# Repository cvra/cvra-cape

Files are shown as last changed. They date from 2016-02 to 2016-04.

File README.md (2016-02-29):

# CVRA cape

A Beaglebone black extension board for robots used at [CVRA](http://www.cvra.ch/).

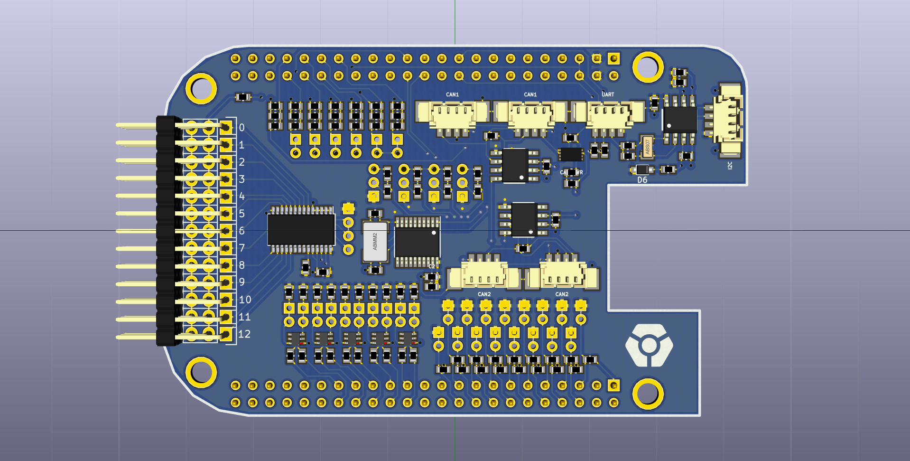
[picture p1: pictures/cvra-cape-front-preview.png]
Board Layout (Front view)

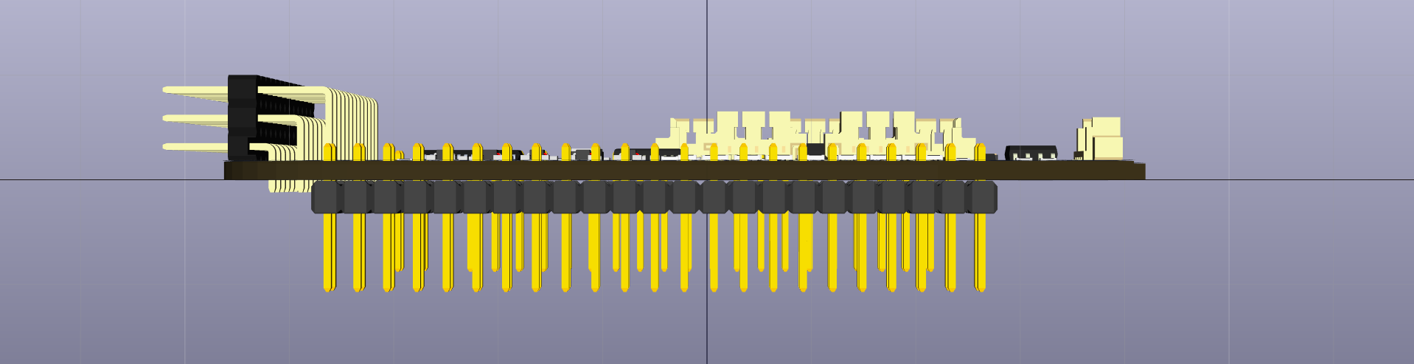
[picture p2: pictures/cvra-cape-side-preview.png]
Board Layout (Side view)


## Features
- 2x CAN interfaces with transceivers
    - 1x over native CAN peripheral
    - 1x over CAN-SPI chip
- 16x PWM outputs (using a PCA9685 chip over I2C)
    - 13x to control servo motors
    - 1x to control an RGB LED
- 7x analog inputs with voltage dividers and option to power (3-pin connector)
    - 1x analog Lidar 1D input
    - 1x battery voltage sense
    - 1x CAN-bus voltage sense
    - 4x free
- 18x digital inputs with voltage dividers and option to power (3-pin connector)
- 10x digital outputs (LEDs) with NPN stage to draw 10-100mA
- Power the BBB over the CAN-bus or over USB (switch)
- 1x I2C connector
- 1x UART connector
- 1x RTC with battery soldered directly on the cape

## Notes

### PWM
The PWM outputs are provided by a PWM chip controlled over I2C (PCA9685).

### CAN
There are 2 CAN interfaces on the cape. We use one. The other CAN uses an SPI (TBD).
- `CAN1` uses the `DCAN1` interface on the Beaglebone
    * `CAN1_RX` is on pin `P9.24`
    * `CAN1_TX` is on pin `P9.26`

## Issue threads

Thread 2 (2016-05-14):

Changes for revB

SyrianSpock, 2016-05-14:
- No 5V CAN bus power protection (too much current limiting, Beaglebone's protection is enough)
- Fix RX/TX inversion on CAN1 tranceiver

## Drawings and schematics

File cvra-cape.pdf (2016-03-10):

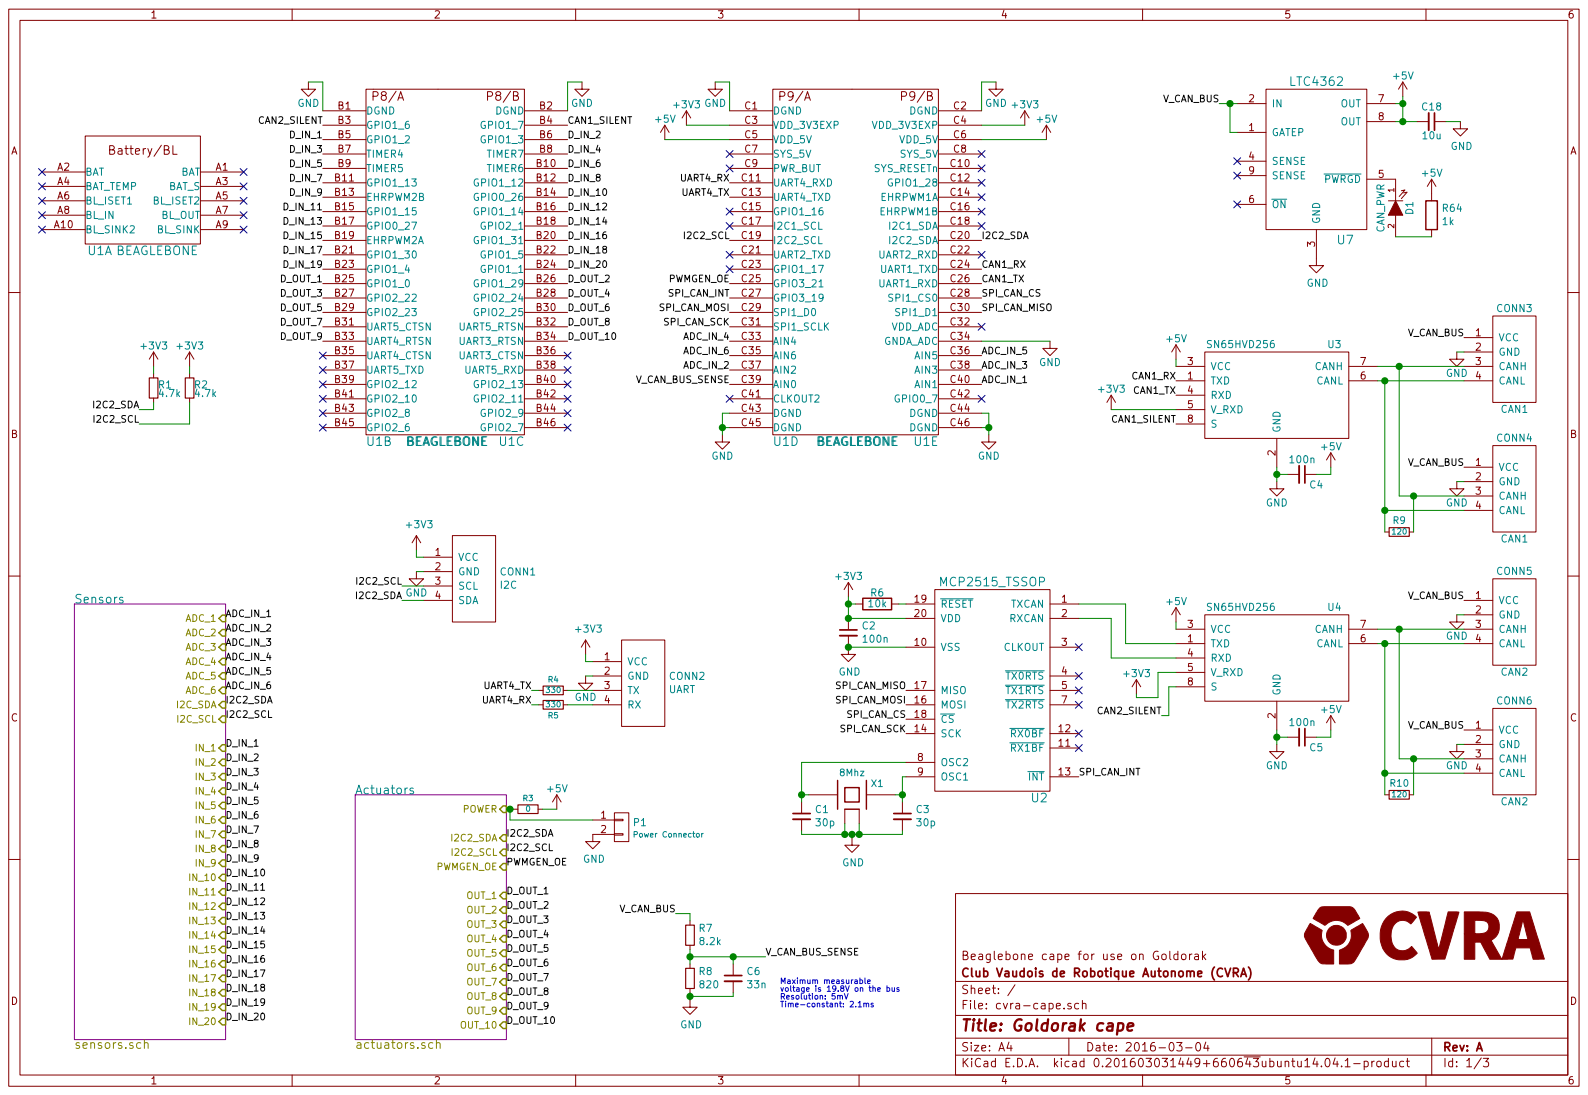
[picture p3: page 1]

3 SENSE 4 PWRGD 5 ON 6 OUT 7 OUT 8 SENSE 9 U7

2 VCC 3 RXD 4 V_RXD 5 CANL 6 CANH 7 S

Beaglebone cape for use on Goldorak
File: cvra-cape.sch Sheet: / Club Vaudois de Robotique Autonome (CVRA)

Maximum measurable voltage is 19.8V on the bus Resolution: 5mV

Id: 1/3 Title: Goldorak cape

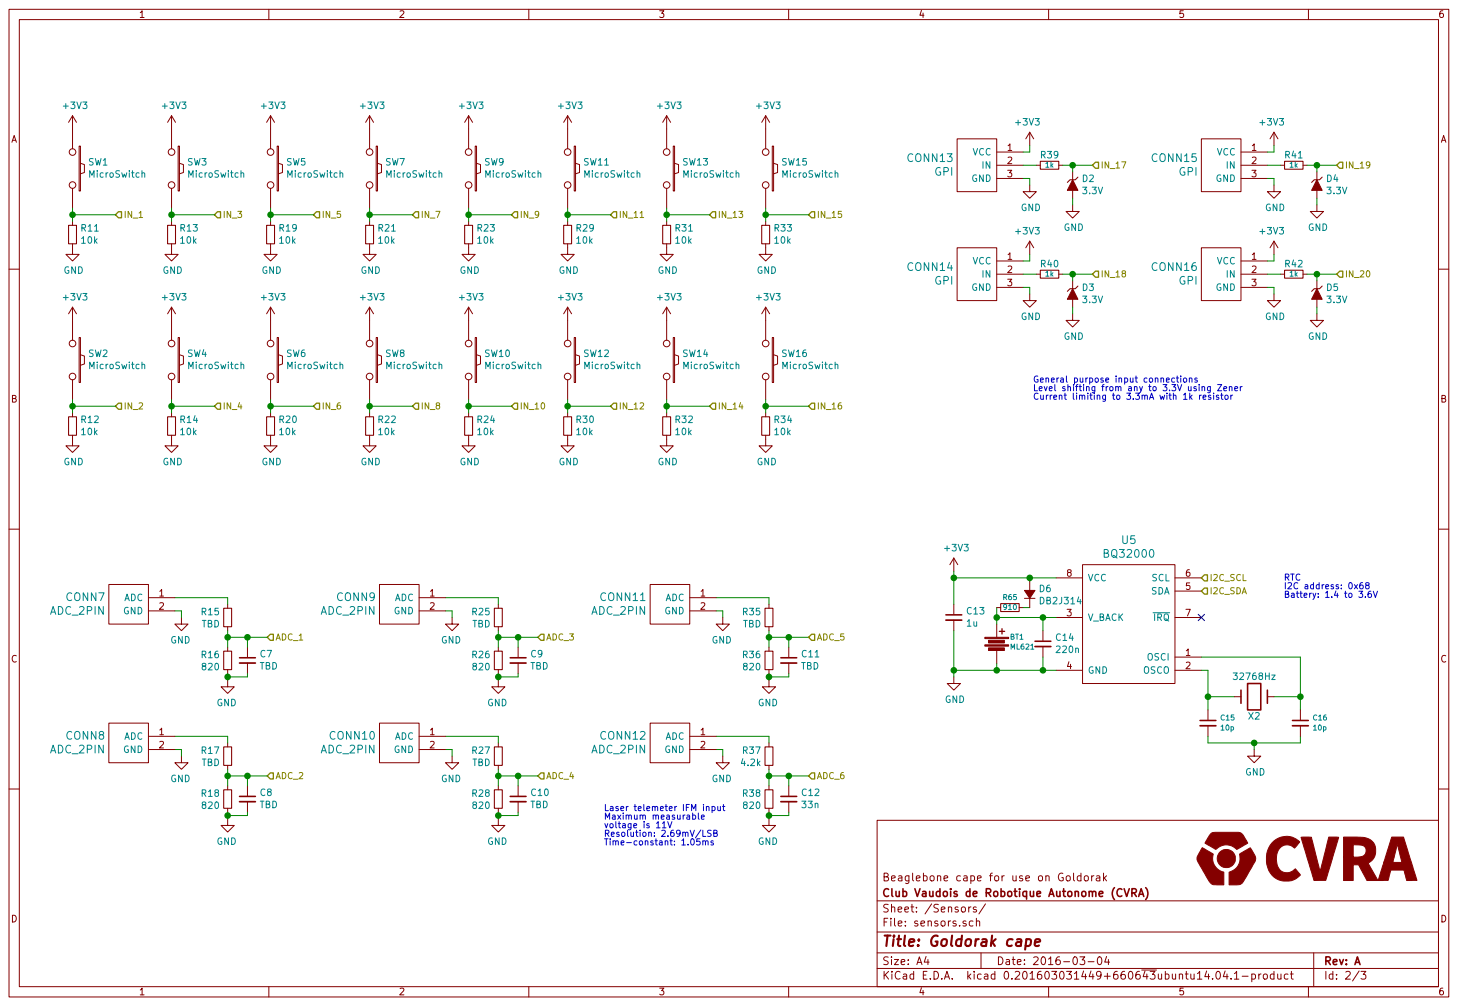
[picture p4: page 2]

IN_18 General purpose input connections Level shifting from any to 3.3V using Zener Current limiting to 3.3mA with 1k resistor C7 TBD

Beaglebone cape for use on Goldorak ADC_1 R15 TBD

Laser telemeter IFM input Maximum measurable
voltage is 11V Resolution: 2.69mV/LSB

File: sensors.sch Sheet: /Sensors/ Club Vaudois de Robotique Autonome (CVRA)

Id: 2/3 Title: Goldorak cape

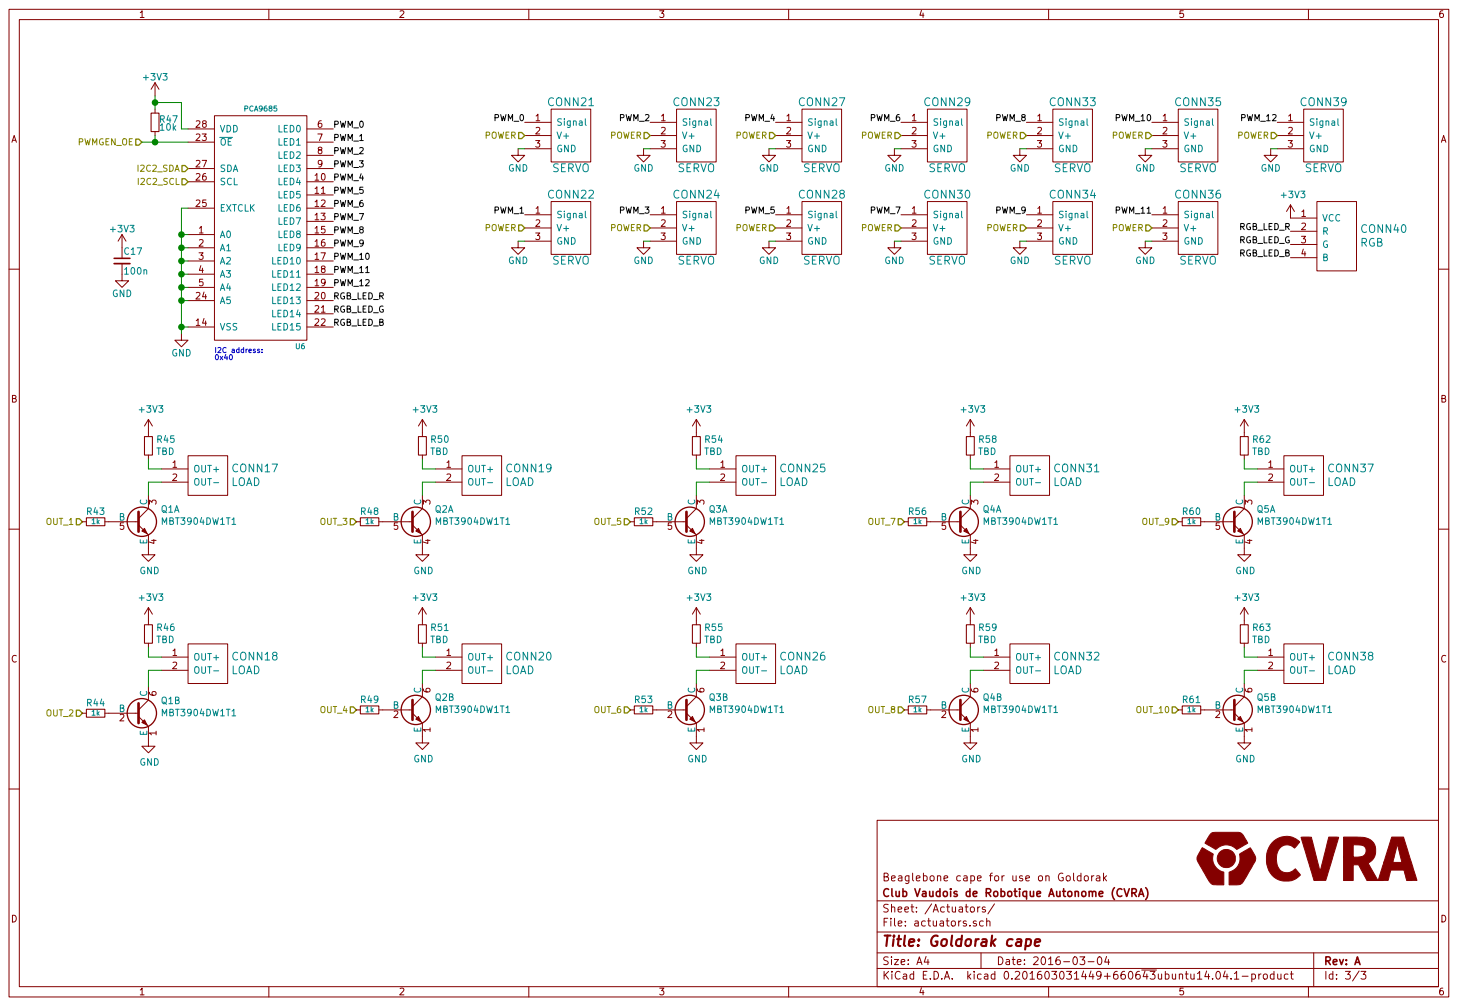
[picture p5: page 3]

Beaglebone cape for use on Goldorak
File: actuators.sch Sheet: /Actuators/ Club Vaudois de Robotique Autonome (CVRA)

Id: 3/3 Title: Goldorak cape

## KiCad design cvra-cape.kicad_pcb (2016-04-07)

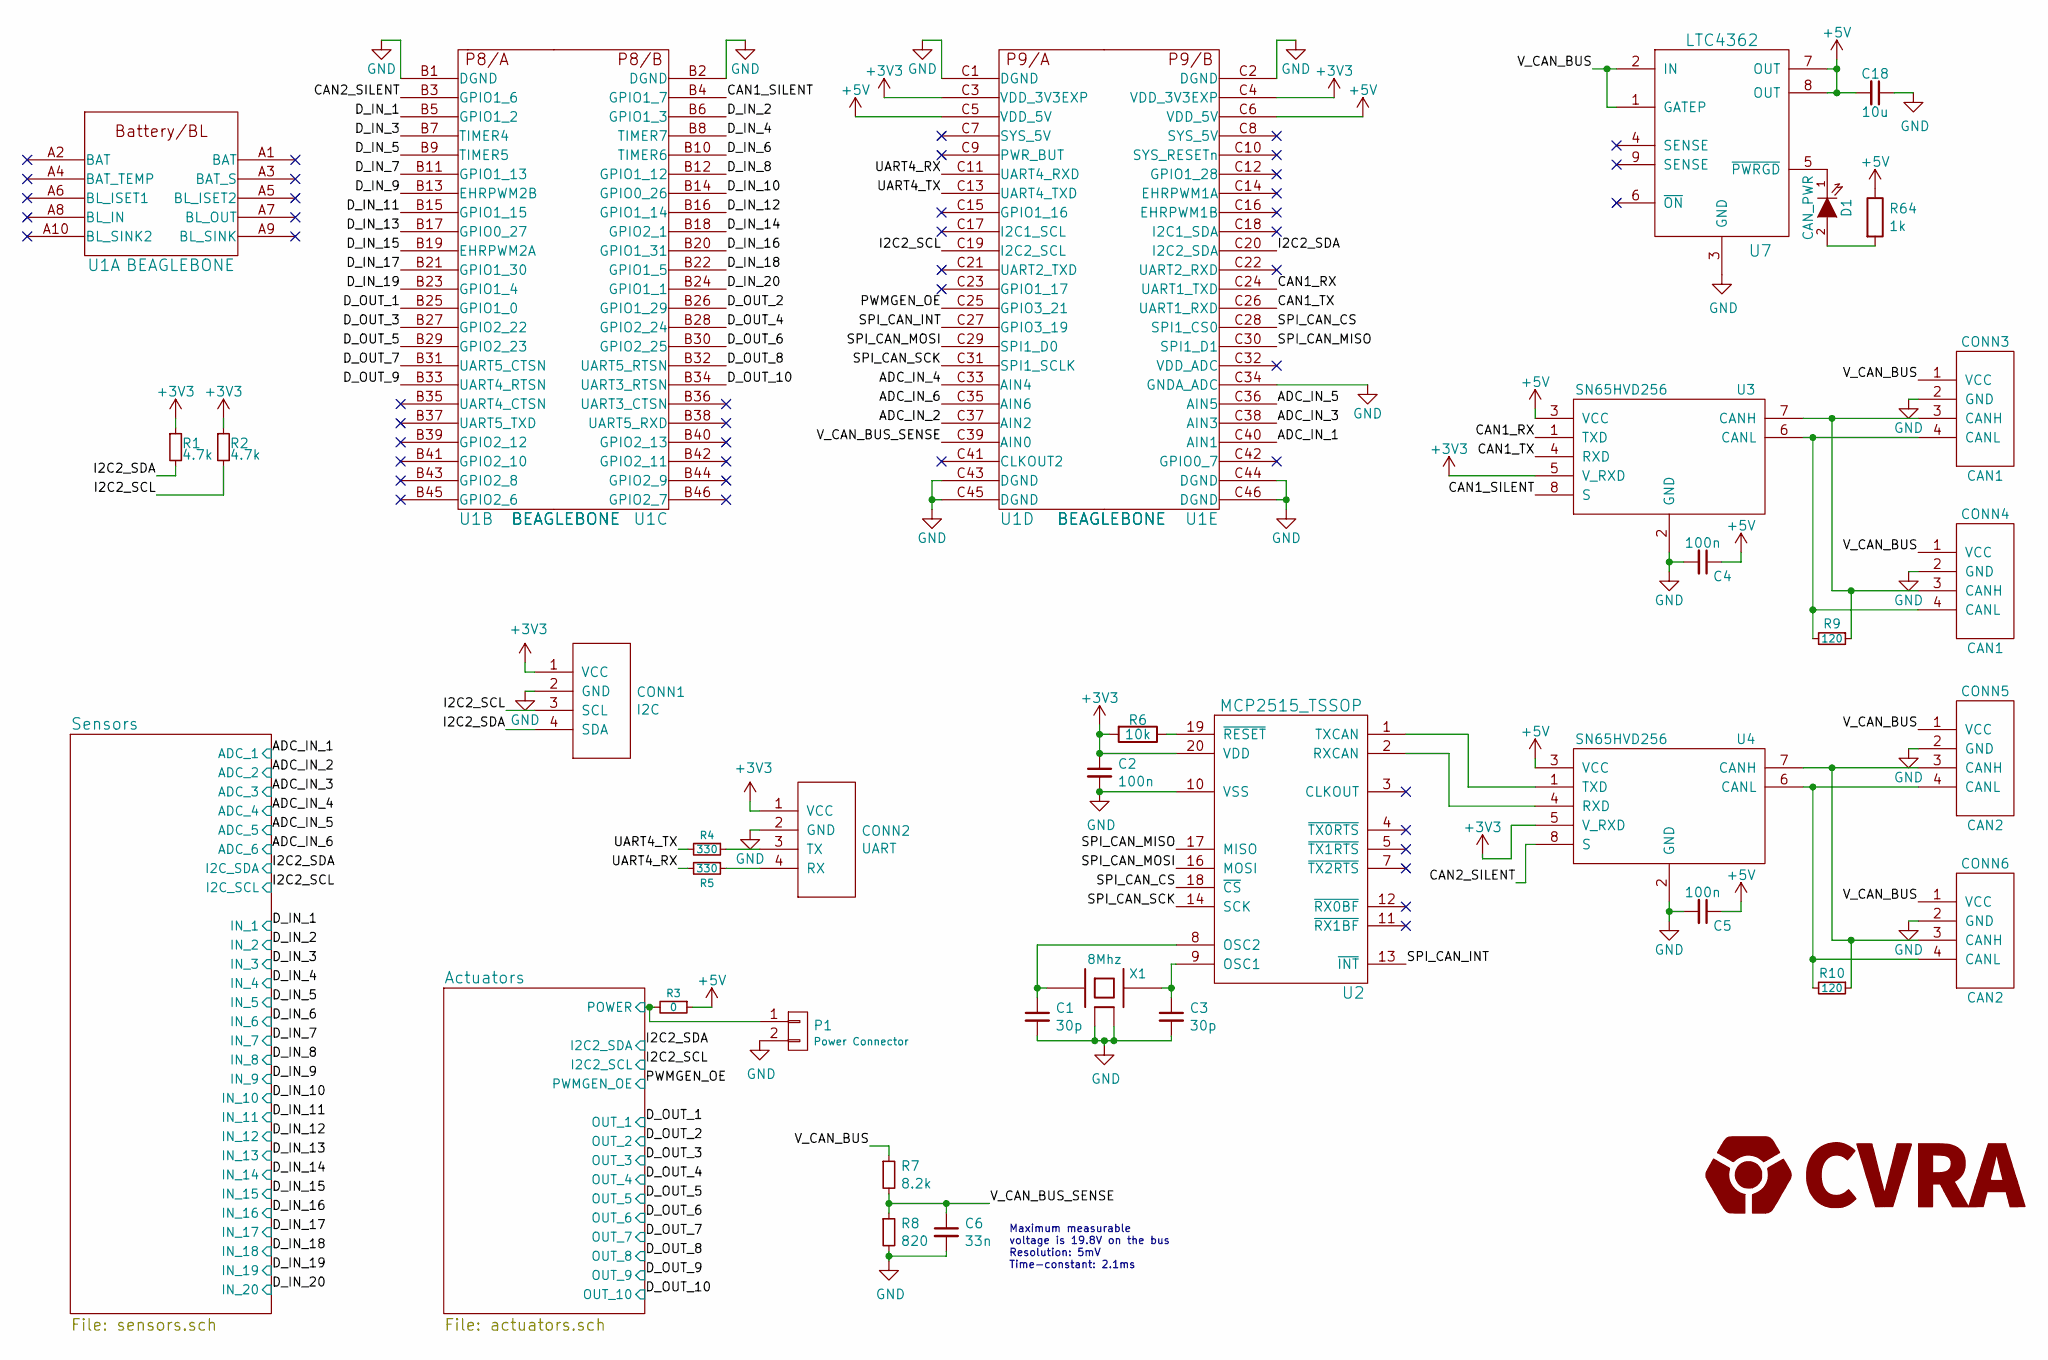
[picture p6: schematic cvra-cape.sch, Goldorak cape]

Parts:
C1, C3: 30p; _0603
C2, C4, C5: 100n; _0603
C6: 33n; _0603
C18: 10u; _0603
CONN1: I2C; _Molex-PicoBlade-SMD-4
CONN2: UART; _Molex-PicoBlade-SMD-4
CONN3, CONN4: CAN1; _Molex-PicoBlade-SMD-4
CONN5, CONN6: CAN2; _Molex-PicoBlade-SMD-4
D1: CAN_PWR; _0603
P1: Power Connector; Pin_Header_Straight_1x02
R1, R2: 4.7k; _0603
R3: 0; _0603
R4, R5: 330; _0603
R6: 10k; _0603
R7: 8.2k; _0603
R8: 820; _0603
R9, R10: 120; _0603
R64: 1k; _0603
U1: BEAGLEBONE
U2: MCP2515_TSSOP; TSSOP-20_4.4x6.5mm_Pitch0.65mm
U3, U4: SN65HVD256; _SO-8
U7: LTC4362; DFN_8-Lead_2mmx3mm
X1: 8Mhz; XTAL_ABMM2

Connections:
+3V3: C2.1, CONN1.1 (VCC), CONN2.1 (VCC), R1.1, R2.1, R6.2, U1.C3 (VDD_3V3EXP), U1.C4 (VDD_3V3EXP), U2.20 (VDD), U3.5 (V_RXD), U4.5 (V_RXD); also elsewhere on the board
+5V: C4.1, C5.1, C18.2, R3.1, R64.1, U1.C5 (VDD_5V), U1.C6 (VDD_5V), U3.3 (VCC), U4.3 (VCC), U7.7 (OUT), U7.8 (OUT)
/ADC_IN_1: U1.C40 (AIN1); also elsewhere on the board
/ADC_IN_2: U1.C37 (AIN2); also elsewhere on the board
/ADC_IN_3: U1.C38 (AIN3); also elsewhere on the board
/ADC_IN_4: U1.C33 (AIN4); also elsewhere on the board
/ADC_IN_5: U1.C36 (AIN5); also elsewhere on the board
/ADC_IN_6: U1.C35 (AIN6); also elsewhere on the board
/Actuators/POWER: P1.1, R3.2; also elsewhere on the board
/CAN1_RX: U1.C24 (UART1_TXD), U3.1 (TXD)
/CAN1_SILENT: U1.B4 (GPIO1_7), U3.8 (S)
/CAN1_TX: U1.C26 (UART1_RXD), U3.4 (RXD)
/CAN2_SILENT: U1.B3 (GPIO1_6), U4.8 (S)
/D_IN_1: U1.B5 (GPIO1_2); also elsewhere on the board
/D_IN_2: U1.B6 (GPIO1_3); also elsewhere on the board
/D_IN_3: U1.B7 (TIMER4); also elsewhere on the board
/D_IN_4: U1.B8 (TIMER7); also elsewhere on the board
/D_IN_5: U1.B9 (TIMER5); also elsewhere on the board
/D_IN_6: U1.B10 (TIMER6); also elsewhere on the board
/D_IN_7: U1.B11 (GPIO1_13); also elsewhere on the board
/D_IN_8: U1.B12 (GPIO1_12); also elsewhere on the board
/D_IN_9: U1.B13 (EHRPWM2B); also elsewhere on the board
/D_IN_10: U1.B14 (GPIO0_26); also elsewhere on the board
/D_IN_11: U1.B15 (GPIO1_15); also elsewhere on the board
/D_IN_12: U1.B16 (GPIO1_14); also elsewhere on the board
/D_IN_13: U1.B17 (GPIO0_27); also elsewhere on the board
/D_IN_14: U1.B18 (GPIO2_1); also elsewhere on the board
/D_IN_15: U1.B19 (EHRPWM2A); also elsewhere on the board
/D_IN_16: U1.B20 (GPIO1_31); also elsewhere on the board
/D_IN_17: U1.B21 (GPIO1_30); also elsewhere on the board
/D_IN_18: U1.B22 (GPIO1_5); also elsewhere on the board
/D_IN_19: U1.B23 (GPIO1_4); also elsewhere on the board
/D_IN_20: U1.B24 (GPIO1_1); also elsewhere on the board
/D_OUT_1: U1.B25 (GPIO1_0); also elsewhere on the board
/D_OUT_2: U1.B26 (GPIO1_29); also elsewhere on the board
/D_OUT_3: U1.B27 (GPIO2_22); also elsewhere on the board
/D_OUT_4: U1.B28 (GPIO2_24); also elsewhere on the board
/D_OUT_5: U1.B29 (GPIO2_23); also elsewhere on the board
/D_OUT_6: U1.B30 (GPIO2_25); also elsewhere on the board
/D_OUT_7: U1.B31 (UART5_CTSN); also elsewhere on the board
/D_OUT_8: U1.B32 (UART5_RTSN); also elsewhere on the board
/D_OUT_9: U1.B33 (UART4_RTSN); also elsewhere on the board
/D_OUT_10: U1.B34 (UART3_RTSN); also elsewhere on the board
/I2C2_SCL: CONN1.3 (SCL), R2.2, U1.C19 (I2C2_SCL); also elsewhere on the board
/I2C2_SDA: CONN1.4 (SDA), R1.2, U1.C20 (I2C2_SDA); also elsewhere on the board
/PWMGEN_OE: U1.C25 (GPIO3_21); also elsewhere on the board
/SPI_CAN_CS: U1.C28 (SPI1_CS0), U2.18 (~CS)
/SPI_CAN_INT: U1.C27 (GPIO3_19), U2.13 (~INT)
/SPI_CAN_MISO: U1.C30 (SPI1_D1), U2.17 (MISO)
/SPI_CAN_MOSI: U1.C29 (SPI1_D0), U2.16 (MOSI)
/SPI_CAN_SCK: U1.C31 (SPI1_SCLK), U2.14 (SCK)
/UART4_RX: R5.2, U1.C11 (UART4_RXD)
/UART4_TX: R4.2, U1.C13 (UART4_TXD)
/V_CAN_BUS: CONN3.1 (VCC), CONN4.1 (VCC), CONN5.1 (VCC), CONN6.1 (VCC), R7.1, U7.1 (GATEP), U7.2 (IN)
/V_CAN_BUS_SENSE: C6.1, R7.2, R8.1, U1.C39 (AIN0)
GND: C1.2, C2.2, C3.2, C4.2, C5.2, C6.2, C18.1, CONN1.2 (GND), CONN1.MECH (GND), CONN2.2 (GND), CONN2.MECH (GND), CONN3.2 (GND), CONN3.MECH (GND), CONN4.2 (GND), CONN4.MECH (GND), CONN5.2 (GND), CONN5.MECH (GND), CONN6.2 (GND), CONN6.MECH (GND), P1.2, R8.2, U1.B1 (DGND), U1.B2 (DGND), U1.C1 (DGND), U1.C2 (DGND), U1.C34 (GNDA_ADC), U1.C43 (DGND), U1.C44 (DGND), U1.C45 (DGND), U1.C46 (DGND), U2.10 (VSS), U3.2 (GND), U4.2 (GND), U7.3 (GND), X1.2 (case), X1.4 (case); also elsewhere on the board
unnamed: C1.1, U2.8 (OSC2), X1.1
unnamed: C3.1, U2.9 (OSC1), X1.3
unnamed: CONN2.3 (TX), R4.1
unnamed: CONN2.4 (RX), R5.1
unnamed: CONN3.3 (CANH), CONN4.3 (CANH), R9.1, U3.7 (CANH)
unnamed: CONN3.4 (CANL), CONN4.4 (CANL), R9.2, U3.6 (CANL)
unnamed: CONN5.3 (CANH), CONN6.3 (CANH), R10.1, U4.7 (CANH)
unnamed: CONN5.4 (CANL), CONN6.4 (CANL), R10.2, U4.6 (CANL)
unnamed: D1.1 (K), U7.5 (~PWRGD)
unnamed: D1.2 (A), R64.2
unnamed: R6.1, U2.19 (~RESET)
unnamed: U2.1 (TXCAN), U4.1 (TXD)
unnamed: U2.2 (RXCAN), U4.4 (RXD)

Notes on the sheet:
Maximum measurable voltage is 19.8V on the bus Resolution: 5mV Time-constant: 2.1ms

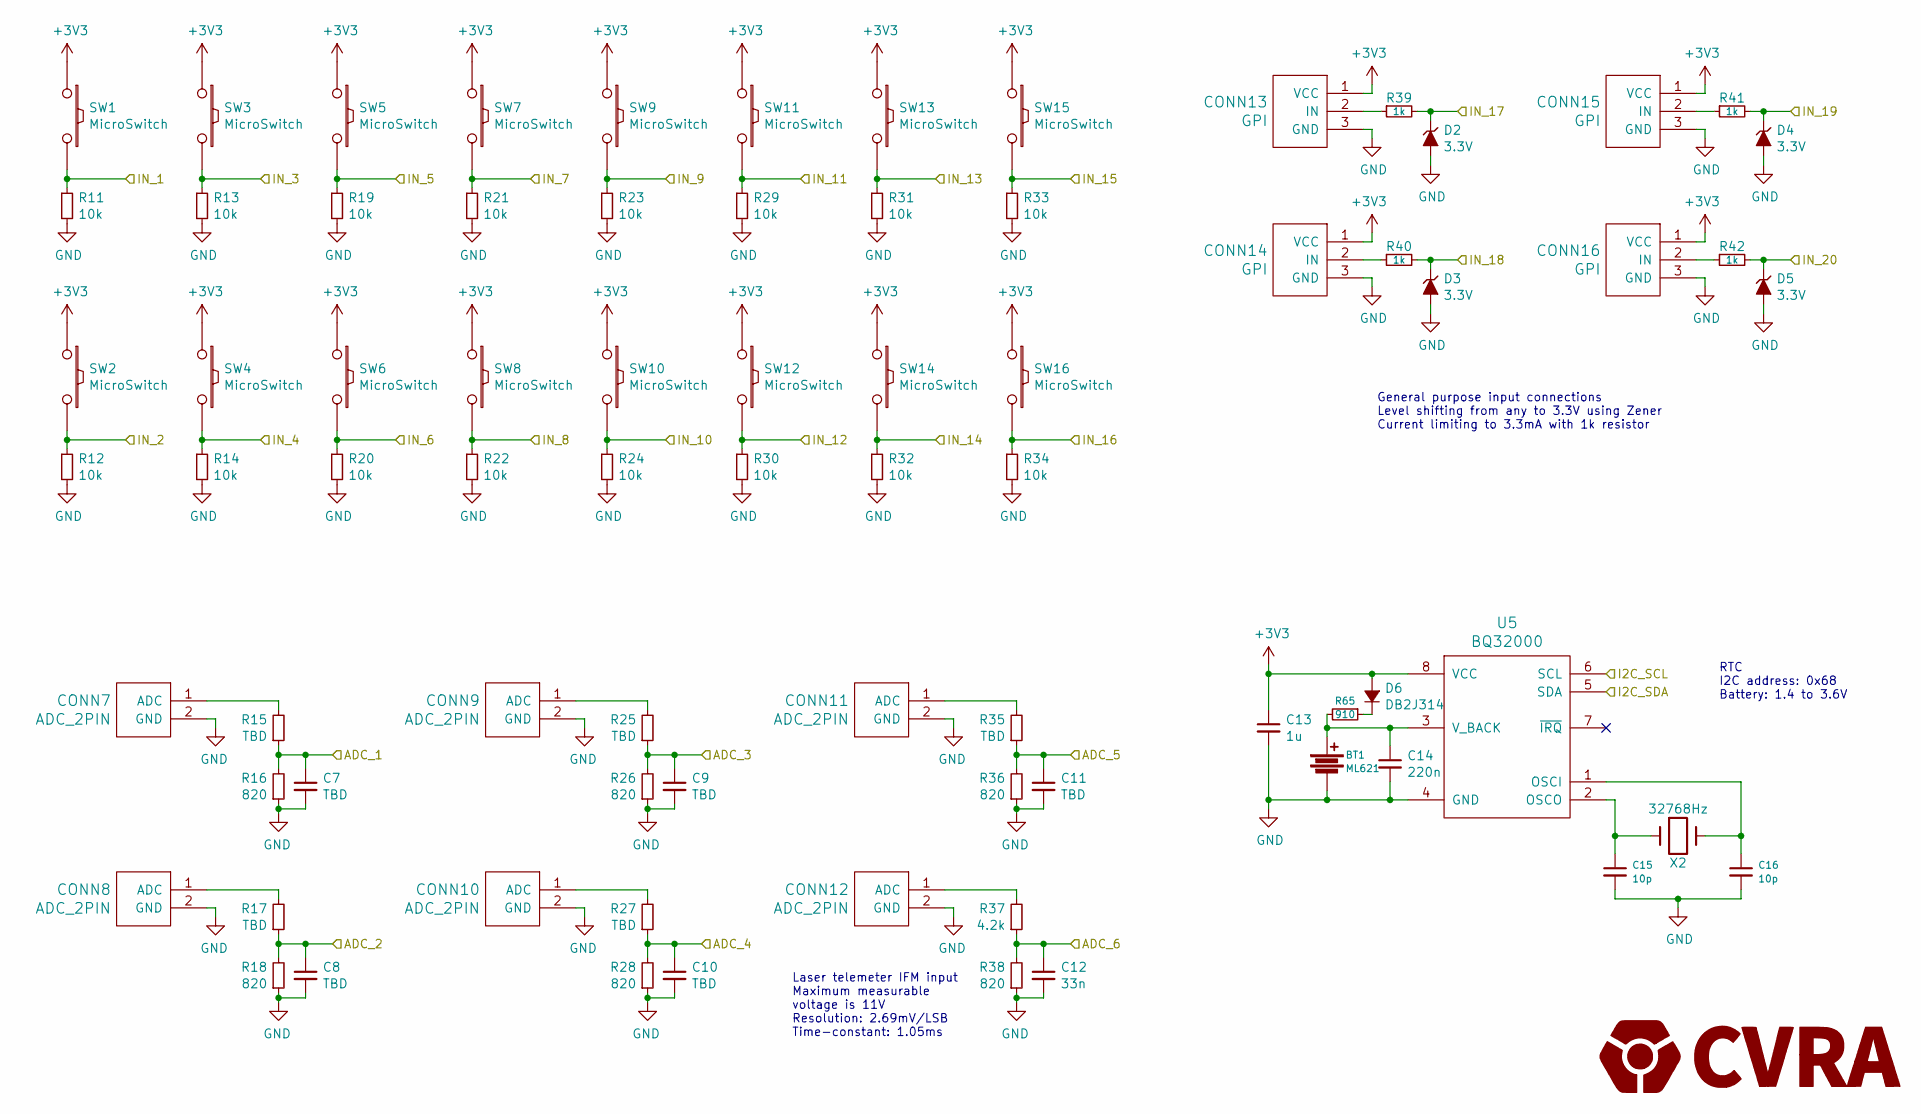
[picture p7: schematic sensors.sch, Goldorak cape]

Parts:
BT1: ML621; Battery_ML621
C7, C8, C9, C10, C11: TBD; _0603
C12: 33n; _0603
C13: 1u; _0603
C14: 220n; _0603
C15, C16: 10p; _0603
CONN7, CONN8, CONN9, CONN10, CONN11, CONN12: ADC_2PIN; _Pin2mm_2
CONN13, CONN14, CONN15, CONN16: GPI; _Pin2mm_3
D2, D3, D4, D5: 3.3V; _0603
D6: DB2J314; Diode_SMini2
R11, R12, R13, R14, R19, R20, R21, R22, R23, R24, R29, R30, R31, R32, R33, R34: 10k; _0603
R15, R17, R25, R27, R35: TBD; _0603
R16, R18, R26, R28, R36, R38: 820; _0603
R37: 4.2k; _0603
R39, R40, R41, R42: 1k; _0603
R65: 910; _0603
SW1, SW2, SW3, SW4, SW5, SW6, SW7, SW8, SW9, SW10, SW11, SW12, SW13, SW14, SW15, SW16: MicroSwitch; _Pin2mm_2
U5: BQ32000; _SO-8
X2: 32768Hz; XTAL_ABS07

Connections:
+3V3: C13.1, CONN13.1 (VCC), CONN14.1 (VCC), CONN15.1 (VCC), CONN16.1 (VCC), D6.2 (A), SW1.1, SW2.1, SW3.1, SW4.1, SW5.1, SW6.1, SW7.1, SW8.1, SW9.1, SW10.1, SW11.1, SW12.1, SW13.1, SW14.1, SW15.1, SW16.1, U5.8 (VCC); also elsewhere on the board
/ADC_IN_1: C7.1, R15.1, R16.2; also elsewhere on the board
/ADC_IN_2: C8.1, R17.1, R18.2; also elsewhere on the board
/ADC_IN_3: C9.1, R25.1, R26.2; also elsewhere on the board
/ADC_IN_4: C10.1, R27.1, R28.2; also elsewhere on the board
/ADC_IN_5: C11.1, R35.1, R36.2; also elsewhere on the board
/ADC_IN_6: C12.1, R37.1, R38.2; also elsewhere on the board
/D_IN_1: R11.1, SW1.2; also elsewhere on the board
/D_IN_2: R12.1, SW2.2; also elsewhere on the board
/D_IN_3: R13.1, SW3.2; also elsewhere on the board
/D_IN_4: R14.1, SW4.2; also elsewhere on the board
/D_IN_5: R19.1, SW5.2; also elsewhere on the board
/D_IN_6: R20.1, SW6.2; also elsewhere on the board
/D_IN_7: R21.1, SW7.2; also elsewhere on the board
/D_IN_8: R22.1, SW8.2; also elsewhere on the board
/D_IN_9: R23.1, SW9.2; also elsewhere on the board
/D_IN_10: R24.1, SW10.2; also elsewhere on the board
/D_IN_11: R29.1, SW11.2; also elsewhere on the board
/D_IN_12: R30.1, SW12.2; also elsewhere on the board
/D_IN_13: R31.1, SW13.2; also elsewhere on the board
/D_IN_14: R32.1, SW14.2; also elsewhere on the board
/D_IN_15: R33.1, SW15.2; also elsewhere on the board
/D_IN_16: R34.1, SW16.2; also elsewhere on the board
/D_IN_17: D2.1 (K), R39.2; also elsewhere on the board
/D_IN_18: D3.1 (K), R40.2; also elsewhere on the board
/D_IN_19: D4.1 (K), R41.2; also elsewhere on the board
/D_IN_20: D5.1 (K), R42.2; also elsewhere on the board
/I2C2_SCL: U5.6 (SCL); also elsewhere on the board
/I2C2_SDA: U5.5 (SDA); also elsewhere on the board
GND: BT1.2, C7.2, C8.2, C9.2, C10.2, C11.2, C12.2, C13.2, C14.2, C15.2, C16.2, CONN7.2 (GND), CONN8.2 (GND), CONN9.2 (GND), CONN10.2 (GND), CONN11.2 (GND), CONN12.2 (GND), CONN13.3 (GND), CONN14.3 (GND), CONN15.3 (GND), CONN16.3 (GND), D2.2 (A), D3.2 (A), D4.2 (A), D5.2 (A), R11.2, R12.2, R13.2, R14.2, R16.1, R18.1, R19.2, R20.2, R21.2, R22.2, R23.2, R24.2, R26.1, R28.1, R29.2, R30.2, R31.2, R32.2, R33.2, R34.2, R36.1, R38.1, U5.4 (GND); also elsewhere on the board
unnamed: BT1.1, C14.1, R65.2, U5.3 (V_BACK)
unnamed: C15.1, U5.2 (OSCO), X2.1
unnamed: C16.1, U5.1 (OSCI), X2.2
unnamed: CONN7.1 (ADC), R15.2
unnamed: CONN8.1 (ADC), R17.2
unnamed: CONN9.1 (ADC), R25.2
unnamed: CONN10.1 (ADC), R27.2
unnamed: CONN11.1 (ADC), R35.2
unnamed: CONN12.1 (ADC), R37.2
unnamed: CONN13.2 (IN), R39.1
unnamed: CONN14.2 (IN), R40.1
unnamed: CONN15.2 (IN), R41.1
unnamed: CONN16.2 (IN), R42.1
unnamed: D6.1 (K), R65.1

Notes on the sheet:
RTC I2C address: 0x68 Battery: 1.4 to 3.6V
Laser telemeter IFM input Maximum measurable voltage is 11V Resolution: 2.69mV/LSB Time-constant: 1.05ms
General purpose input connections Level shifting from any to 3.3V using Zener Current limiting to 3.3mA with 1k resistor

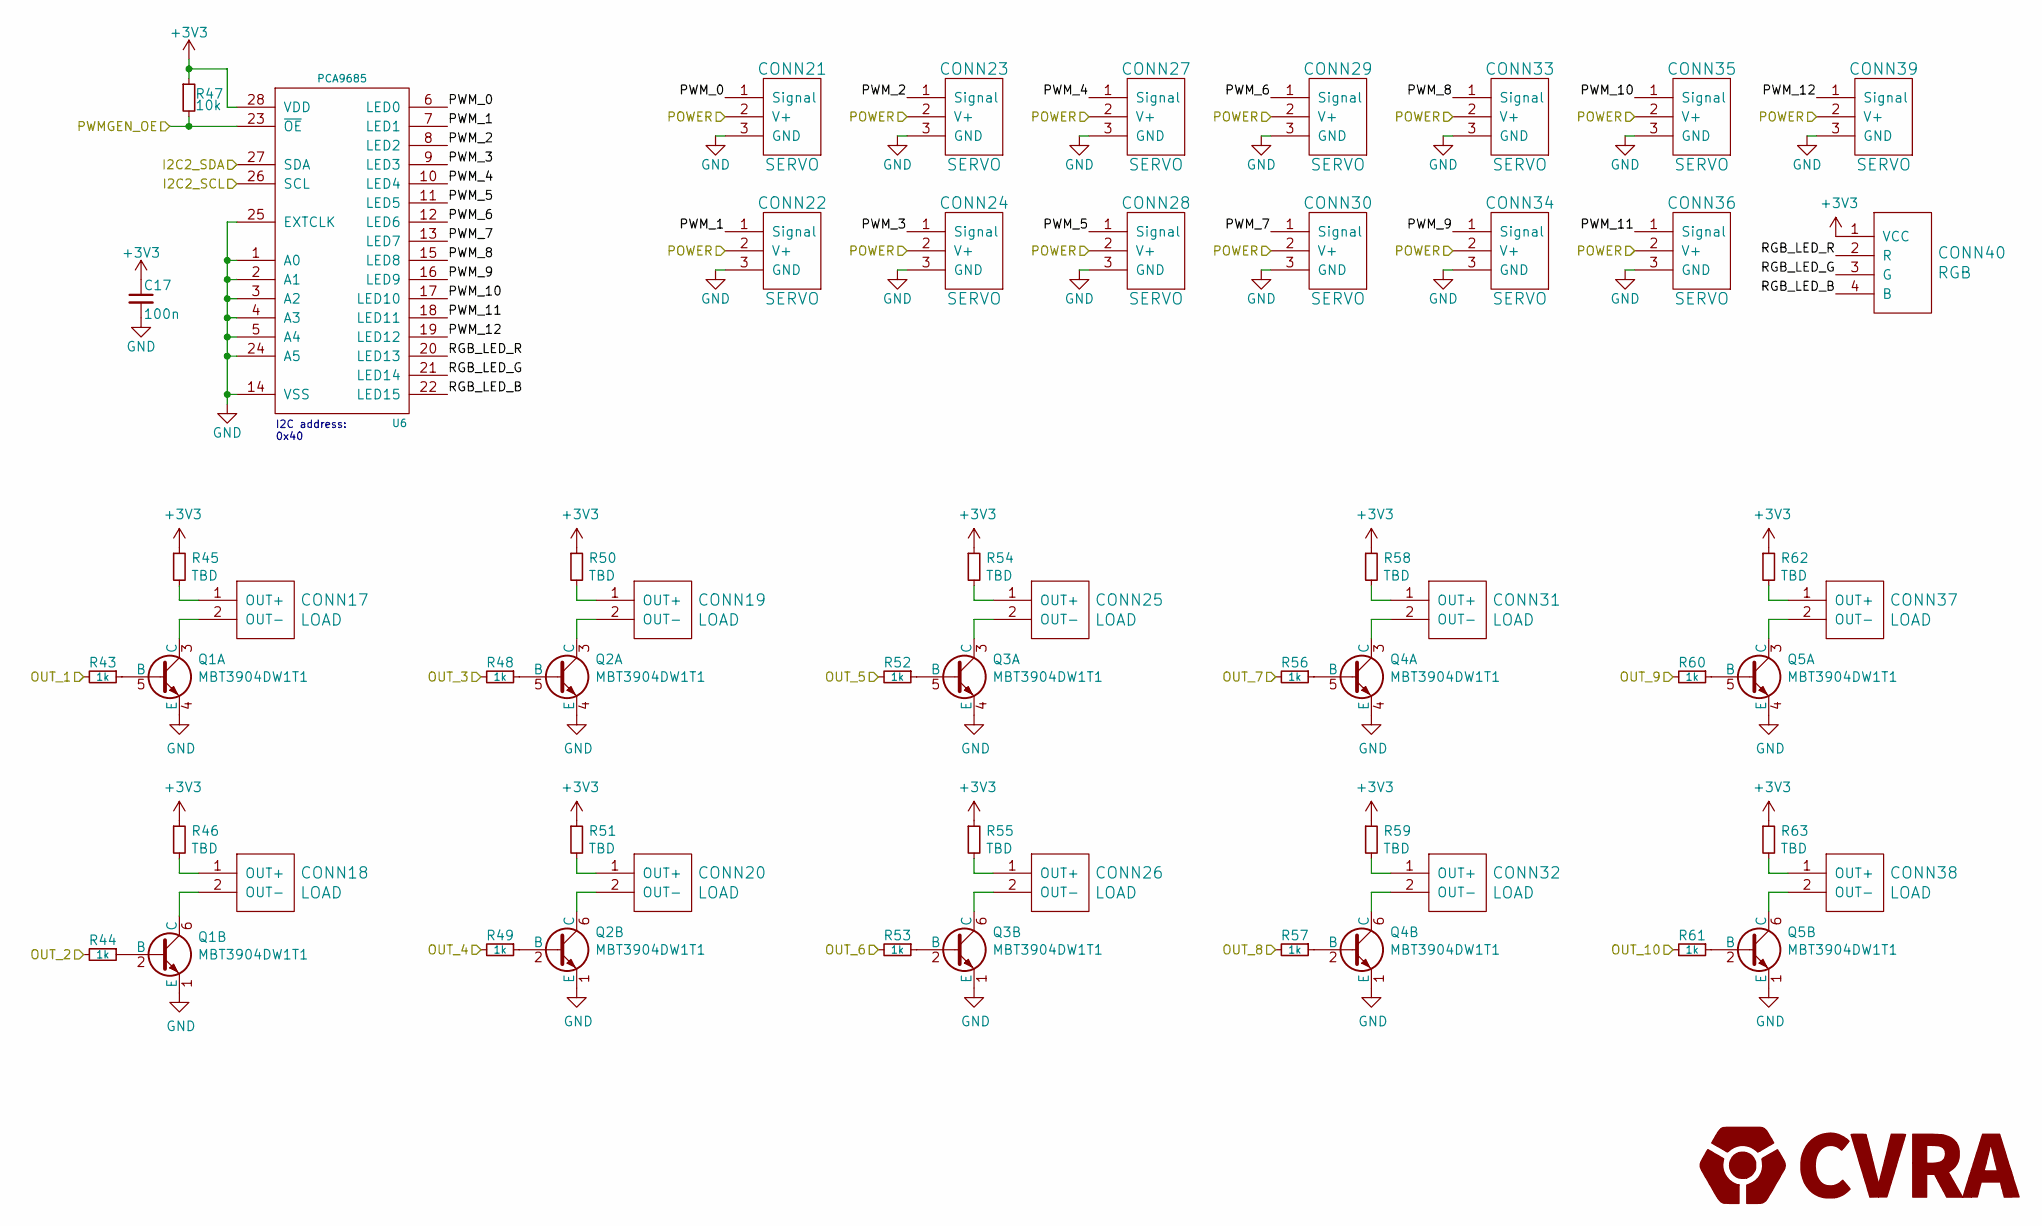
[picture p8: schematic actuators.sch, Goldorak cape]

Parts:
C17: 100n; _0603
CONN17, CONN18, CONN19, CONN20, CONN25, CONN26, CONN31, CONN32, CONN37, CONN38: LOAD; _Pin2mm_2
CONN21, CONN22, CONN23, CONN24, CONN27, CONN28, CONN29, CONN30, CONN33, CONN34, CONN35, CONN36, CONN39: SERVO; Pin_Header_Straight_1x03
CONN40: RGB; _Pin2mm_4
Q1, Q2, Q3, Q4, Q5: MBT3904DW1T1; SOT363
R43, R44, R48, R49, R52, R53, R56, R57, R60, R61: 1k; _0603
R45, R46, R50, R51, R54, R55, R58, R59, R62, R63: TBD; _0603
R47: 10k; _0603
U6: PCA9685; TSSOP-28_4.4x9.7mm_Pitch0.65mm

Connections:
+3V3: C17.1, CONN40.1 (VCC), R45.1, R46.1, R47.1, R50.1, R51.1, R54.1, R55.1, R58.1, R59.1, R62.1, R63.1, U6.28 (VDD); also elsewhere on the board
/Actuators/PWM_0: CONN21.1 (Signal), U6.6 (LED0); also elsewhere on the board
/Actuators/PWM_1: CONN22.1 (Signal), U6.7 (LED1); also elsewhere on the board
/Actuators/PWM_2: CONN23.1 (Signal), U6.8 (LED2); also elsewhere on the board
/Actuators/PWM_3: CONN24.1 (Signal), U6.9 (LED3); also elsewhere on the board
/Actuators/PWM_4: CONN27.1 (Signal), U6.10 (LED4); also elsewhere on the board
/Actuators/PWM_5: CONN28.1 (Signal), U6.11 (LED5); also elsewhere on the board
/Actuators/PWM_6: CONN29.1 (Signal), U6.12 (LED6); also elsewhere on the board
/Actuators/PWM_7: CONN30.1 (Signal), U6.13 (LED7); also elsewhere on the board
/Actuators/PWM_8: CONN33.1 (Signal), U6.15 (LED8); also elsewhere on the board
/Actuators/PWM_9: CONN34.1 (Signal), U6.16 (LED9); also elsewhere on the board
/Actuators/PWM_10: CONN35.1 (Signal), U6.17 (LED10); also elsewhere on the board
/Actuators/PWM_11: CONN36.1 (Signal), U6.18 (LED11); also elsewhere on the board
/Actuators/PWM_12: CONN39.1 (Signal), U6.19 (LED12); also elsewhere on the board
/Actuators/RGB_LED_B: CONN40.4 (B), U6.22 (LED15)
/Actuators/RGB_LED_G: CONN40.3 (G), U6.21 (LED14)
/Actuators/RGB_LED_R: CONN40.2 (R), U6.20 (LED13)
/D_OUT_1: R43.2; also elsewhere on the board
/D_OUT_2: R44.2; also elsewhere on the board
/D_OUT_3: R48.2; also elsewhere on the board
/D_OUT_4: R49.2; also elsewhere on the board
/D_OUT_5: R52.2; also elsewhere on the board
/D_OUT_6: R53.2; also elsewhere on the board
/D_OUT_7: R56.2; also elsewhere on the board
/D_OUT_8: R57.2; also elsewhere on the board
/D_OUT_9: R60.2; also elsewhere on the board
/D_OUT_10: R61.2; also elsewhere on the board
/I2C2_SCL: U6.26 (SCL); also elsewhere on the board
/I2C2_SDA: U6.27 (SDA); also elsewhere on the board
/PWMGEN_OE: R47.2, U6.23 (~OE); also elsewhere on the board
GND: C17.2, CONN21.3 (GND), CONN22.3 (GND), CONN23.3 (GND), CONN24.3 (GND), CONN27.3 (GND), CONN28.3 (GND), CONN29.3 (GND), CONN30.3 (GND), CONN33.3 (GND), CONN34.3 (GND), CONN35.3 (GND), CONN36.3 (GND), CONN39.3 (GND), Q1.1 (E), Q1.4 (E), Q2.1 (E), Q2.4 (E), Q3.1 (E), Q3.4 (E), Q4.1 (E), Q4.4 (E), Q5.1 (E), Q5.4 (E), U6.1 (A0), U6.2 (A1), U6.3 (A2), U6.4 (A3), U6.5 (A4), U6.14 (VSS), U6.24 (A5), U6.25 (EXTCLK); also elsewhere on the board
unnamed: CONN17.1 (OUT+), R45.2
unnamed: CONN17.2 (OUT-), Q1.3 (C)
unnamed: CONN18.1 (OUT+), R46.2
unnamed: CONN18.2 (OUT-), Q1.6 (C)
unnamed: CONN19.1 (OUT+), R50.2
unnamed: CONN19.2 (OUT-), Q2.3 (C)
unnamed: CONN20.1 (OUT+), R51.2
unnamed: CONN20.2 (OUT-), Q2.6 (C)
unnamed: CONN21.2 (V+), CONN22.2 (V+), CONN23.2 (V+), CONN24.2 (V+), CONN27.2 (V+), CONN28.2 (V+), CONN29.2 (V+), CONN30.2 (V+), CONN33.2 (V+), CONN34.2 (V+), CONN35.2 (V+), CONN36.2 (V+), CONN39.2 (V+)
unnamed: CONN25.1 (OUT+), R54.2
unnamed: CONN25.2 (OUT-), Q3.3 (C)
unnamed: CONN26.1 (OUT+), R55.2
unnamed: CONN26.2 (OUT-), Q3.6 (C)
unnamed: CONN31.1 (OUT+), R58.2
unnamed: CONN31.2 (OUT-), Q4.3 (C)
unnamed: CONN32.1 (OUT+), R59.2
unnamed: CONN32.2 (OUT-), Q4.6 (C)
unnamed: CONN37.1 (OUT+), R62.2
unnamed: CONN37.2 (OUT-), Q5.3 (C)
unnamed: CONN38.1 (OUT+), R63.2
unnamed: CONN38.2 (OUT-), Q5.6 (C)
unnamed: Q1.2 (B), R44.1
unnamed: Q1.5 (B), R43.1
unnamed: Q2.2 (B), R49.1
unnamed: Q2.5 (B), R48.1
unnamed: Q3.2 (B), R53.1
unnamed: Q3.5 (B), R52.1
unnamed: Q4.2 (B), R57.1
unnamed: Q4.5 (B), R56.1
unnamed: Q5.2 (B), R61.1
unnamed: Q5.5 (B), R60.1

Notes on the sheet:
I2C address: 0x40

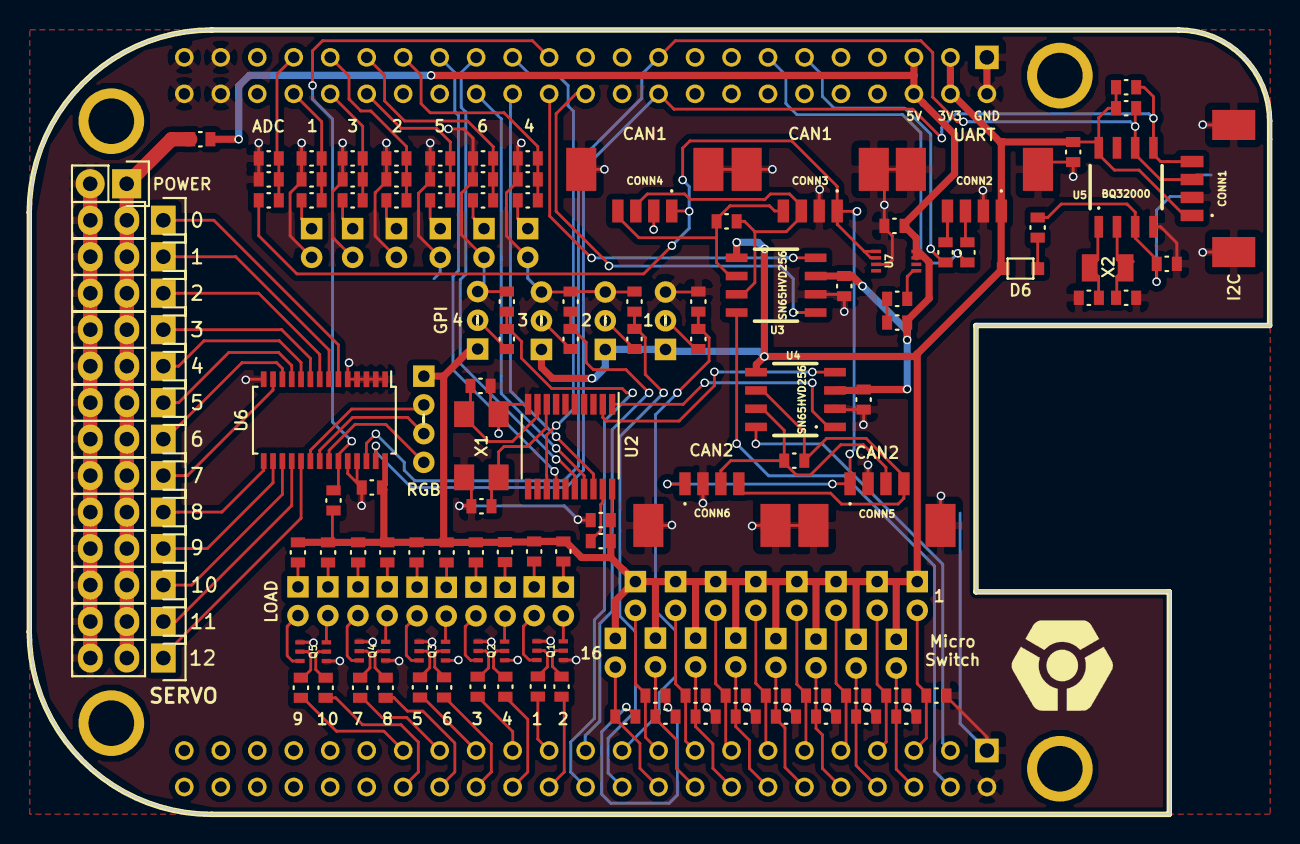
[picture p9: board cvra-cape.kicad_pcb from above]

Board: 2 copper layers, 86.4 x 54.6 mm, 161 parts (1 on the bottom side), 129 nets.

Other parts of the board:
0, 1, 2, 3, 4, 5, 6, 7, 8, 9, 10, 11, 12: SERVO; Pin_Header_Straight_1x03
POWER: Power Connector; Pin_Header_Straight_1x02

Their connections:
/Actuators/POWER: 0.2, 1.2, 2.2, 3.2, 4.2, 5.2, 6.2, 7.2, 8.2, 9.2, 10.2, 11.2, 12.2, POWER.1; also elsewhere on the board
/Actuators/PWM_0: 0.1; also elsewhere on the board
/Actuators/PWM_1: 1.1; also elsewhere on the board
/Actuators/PWM_2: 2.1; also elsewhere on the board
/Actuators/PWM_3: 3.1; also elsewhere on the board
/Actuators/PWM_4: 4.1; also elsewhere on the board
/Actuators/PWM_5: 5.1; also elsewhere on the board
/Actuators/PWM_6: 6.1; also elsewhere on the board
/Actuators/PWM_7: 7.1; also elsewhere on the board
/Actuators/PWM_8: 8.1; also elsewhere on the board
/Actuators/PWM_9: 9.1; also elsewhere on the board
/Actuators/PWM_10: 10.1; also elsewhere on the board
/Actuators/PWM_11: 11.1; also elsewhere on the board
/Actuators/PWM_12: 12.1; also elsewhere on the board
GND: 0.3, 1.3, 2.3, 3.3, 4.3, 5.3, 6.3, 7.3, 8.3, 9.3, 10.3, 11.3, 12.3, POWER.2; also elsewhere on the board

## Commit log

2015-10-28 Add kicad library as submodule
2015-10-28 Setup KiCad project with libraries & readme
    [cvra-cape.kicad_pcb, cvra-cape.sch]
2015-10-28 Add Beaglebone cape component
    [cvra-cape.sch]
2015-10-28 Add PWM outputs
    [cvra-cape.sch]
2015-10-28 Document PWM output pins numbering
2015-10-28 Add CAN interfaces
    [cvra-cape.sch]
2015-10-28 Add components datasheets
    CAN transceiver
    Load switch of CAN bus power
2015-10-28 Add note about CAN interfaces wiring
2015-12-13 Add PWM chip and servo outputs
    [actuators.sch, cvra-cape.sch]
2015-12-22 Add power from CAN bus and switch to hierarchical labelling
    [actuators.sch, cvra-cape.sch]
2016-01-20 Add ADC outputs with voltage dividers
    [actuators.sch, cvra-cape.sch]
2016-02-01 Add CAN over SPI interface using MCP251
    [cvra-cape.sch, sensors.sch]
2016-02-05 Use 3pin connectors for ADC (with power pin)
    [cvra-cape.sch, sensors.sch]
2016-02-05 Add RTC
    [cvra-cape.sch, sensors.sch]
2016-02-08 Add digital inputs with power option
    [cvra-cape.sch, sensors.sch]
2016-02-08 Add digital outputs with NPN stage
    [actuators.sch, cvra-cape.sch]
2016-02-09 Add decoupling capacitors at ADC inputs
    [sensors.sch]
2016-02-12 Add connector for RGB LED
    [actuators.sch]
2016-02-12 Correct digital outputs as we want to drive loads (LEDs)
    [actuators.sch, cvra-cape.sch, sensors.sch]
2016-02-14 Wire inputs from switches correctly
    [cvra-cape.sch, sensors.sch]
2016-02-14 Fix small details & replot pdf
    [actuators.sch, cvra-cape.sch, sensors.sch]
2016-02-20 Correct schematic after review by @vieillemaison
    [actuators.sch]
2016-02-21 Update CAN power protection
    Avoid dropout below 5V by using LTC4362 instead of custom protection with Shottky + Fuse
    The chip provides overcurrent and overvoltage protection
    [actuators.sch, cvra-cape.sch, sensors.sch]
2016-02-27 Add a recharge circuit for the RTC backup battery
    [actuators.sch, cvra-cape.sch, sensors.sch]
2016-02-27 Add CVRA logo to schematic
    [actuators.sch, cvra-cape.sch, sensors.sch]
2016-02-27 Associate footprints
    [actuators.sch, cvra-cape.kicad_pcb, cvra-cape.sch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]
2016-02-28 Place components on PCB
    [actuators.sch, cvra-cape.kicad_pcb, sensors.sch]
2016-02-29 Show PCB preview in readme
2016-03-03 Routing corrections
    - Use GND plane on both sides
    - Route power lines as 0.5mm thickness tracks
    - Cleanup crystals wiring (symetry)
    - Cleanup ADC wiring to avoid crosstalk
    [cvra-cape.kicad_pcb]
2016-03-04 Add Power connector for servos and silkscreen annotations
    [actuators.sch, cvra-cape.kicad_pcb, cvra-cape.sch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]
2016-03-04 Generate gerber files
    [cvra-cape-B.Cu.gbl, cvra-cape-B.Mask.gbs, cvra-cape-B.SilkS.gbo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]
2016-03-10 Final gerber & schematic
    [cvra-cape-B.Cu.gbl, cvra-cape-B.Mask.gbs, cvra-cape-B.SilkS.gbo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]
2016-03-14 rewrite gerber from kicad OS X
    [cvra-cape-B.Cu.gbl, cvra-cape-B.Mask.gbs, cvra-cape-B.SilkS.gbo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]
2016-04-07 Final gerbers
    [cvra-cape-B.Cu.gbl, cvra-cape-B.Mask.gbs, cvra-cape-B.SilkS.gbo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]
